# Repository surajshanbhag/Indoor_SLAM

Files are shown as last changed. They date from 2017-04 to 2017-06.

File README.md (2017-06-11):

# Indoor_SLAM

Project deals with using Raspberry Pi for Stereo Image processing in ROS.   

Please check the  doc/ folder and wiki for Documentation.

src/vision - Code for stereo streamer, receiver, synchronizer and publishing image topics to ROS  
src/control - Code for MOtor control and encoder  
src/auto_scripts - auto run scripts.    
src/model - URDF Model of the robot.

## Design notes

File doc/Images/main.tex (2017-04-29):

\documentclass[10pt]{article}
\usepackage[english]{babel}
\usepackage[utf8x]{inputenc}
\usepackage{amsmath}
\usepackage{graphicx}
\usepackage{caption}
\usepackage[colorinlistoftodos]{todonotes}
\usepackage{indentfirst}
\usepackage{geometry}
\usepackage[section]{placeins}
\usepackage{float}
\geometry{letterpaper, portrait, margin=1in}
\usepackage{hyperref}
\usepackage{subfigure}
\title{Autonomous- Final Report}
\addcontentsline{toc}{section}{References}
\begin{document}

\begin{titlepage}

\newcommand{\HRule}{\rule{\linewidth}{0.5mm}} % Defines a new command for the horizontal lines, change thickness here
\center % Center everything on the page
\textsc{\Large ECE 592-063 Introduction to Autonomous Systems}\\[1.5cm]
\HRule \\[0.4cm]
{ \huge \bfseries Final Report 

Indoor SLAM -2 using Visual SLAM}\\[0.4cm] % Title of your document
\HRule \\[1.5cm]
\begin{minipage}{0.4\textwidth}
\begin{flushleft} \large
\emph{Authors:}\\
Suraj Shanbhag % Your name

Abhishek Ravi	 % Your name

William Burdick-Crow % Your name

Siddharth Ganesh % Your name

\end{flushleft}
\end{minipage}
~
\begin{minipage}{0.4\textwidth}
\begin{flushright} \large
\emph{Mentor:} \\
Dr.Mihail L. Sichitiu % Supervisor's Name
\end{flushright}
\end{minipage}\\[0.5cm]
{\large April 23,2017}\\[2cm] 
 % Include a department/university logo - this will require the graphicx package
 
%----------------------------------------------------------------------------------------
\vfill % Fill the rest of the page with whitespace

\end{titlepage}

\tableofcontents

\listoffigures

\listoftables
\pagebreak
\section{Abstract}
	Incorporating computer vision on any system requires an immense computation power, which increases the cost and size of the system. For small robots and airborne drones it might not always be feasible to add more computation power. In this report we suggest a system where the processing of the stereo camera video feed is offloaded to a remote computer running ROS whose performance can be scaled to match the task. We use a small 2 wheeled robot with the 2 cameras and a Raspberry Pi 3 to stream the stereo video feed to the host computer which performs the tasks. Other challenges like synchronization, calibration and quality of the video are also addressed in the report. The stereo video feed received is used to create a map of the environment and help the robot navigate. This system becomes a good platform to test various Visual SLAM algorithms and we have tested ORBSLAM2 and RTAB.

\section{Introduction}
Although existing technology has made great leaps and bounds in mapping outdoor areas, it still hasn't made much progress in mapping an indoor environment. This is mainly because of the large size of the current robots being used for mapping making them un-traversable in constrained and small spaces. When such a problem arises, it is convenient if we figure out a way to map our entire surroundings so that we can have a reference to work with and make informed decisions. This problem of indoor or constrained SLAM is of extreme importance in disaster management and medical applications. By gaining real world data of these areas we can actually get an insight into the environment, be it a building debris or the inside of the intestines. By implementing visual SLAM on a two wheeled mobile robot we are presenting a case that, the robot need not be as powerful in itself to perform such high computational problems but can act as a carrier of message to a powerful system to solve real world problems.

	Currently there is very little support for using ROS to run remote slam operations. A large part of our project has been, enabling the usage of remote processing on these ROS applications. This allows for increased flexibility, both in type and cost, of the type of vehicle used for capturing images. It will also allows for a much cheaper vehicle, as all that the vehicle is responsible for is streaming the images back to the computer and controlling the robot. Due to the very few requirements that we have for the robot, it is easy to change what platform is used to carry the camera. As long as the robot is capable of streaming video, our project is applicable.

\section{Related work}
Although nobody has published their findings of Visual Stereo SLAM on a Raspberry pi, we found a work on monocular SLAM using Raspberry pi camera module.\footnote{\href{https://courses.cit.cornell.edu/ece6930/ECE6930\_Spring16\_Final\_MEng\_Reports/SLAM/Real-time\%20ROSberryPi\%20SLAM\%20Robot.pdf}{https://courses.cit.cornell.edu/ece6930/ECE6930\_Spring16\_Final\_MEng\_Reports/SLAM/Real-time\%20ROSberryPi\%20SLAM\%20Robot.pdf}}
This work basically revolves around using a raspberry pi+ camera module on a two wheeled robot of raspberry pi for loop detections and re-localization using ORBSLAM while streaming at a much low image quality for a single camera to find loop closure and odometry. Monocular SLAM can be handled by a raspberry pi, but streaming two video streams for stereo ORBSLAM is complex. There is extensive research and findings publicly available for pre-built stereo cameras but none for an assembled stereo camera setup using two monocular USB cameras. People have eliminated the use of two USB Cameras connected to a pi by using the Pi compute module. This eliminated the time synchronization issues and gives a very good image resolution.\footnote{\href{http://hackaday.com/2014/11/03/stereo-vision-and-depth-mapping-with-two-raspi-camera-modules/} {http://hackaday.com/2014/11/03/stereo-vision-and-depth-mapping-with-two-raspi-camera-modules/}} An already implemented SLAM algorithm for Stereo Outdoor mapping  \footnote{\href{http://wiki.ros.org/rtabmap\_ros}{http://wiki.ros.org/rtabmap\_ros}} served as a guide for our project to implement a low cost Indoor stereo SLAM. RTABMap (Real Time Appearance Based Mapping) is used widely to reconstruct our 3D environment. It has been deployed using a bumblebee stereo camera.\footnote{\href{http://wiki.ros.org/rtabmap\_ros/Tutorials/StereoOutdoorMapping}{http://wiki.ros.org/rtabmap\_ros/Tutorials/StereoOutdoorMapping}} 

\section{Approach}
We stated with a robot module that had two servo motors and corresponding encoders. On it we mounted the raspberry pi, two Logitech c920 web cams, a motor control hat, and a pair of power supplies (one for the pi and one for the motors). 
\subsection{Video streaming from Raspberry pi}
We started with Raspbian installed on the Pi.\footnote{\href{https://www.raspberrypi.org/downloads/raspbian/}{https://www.raspberrypi.org/downloads/raspbian/}} However, we were unable to install the uvc\_cam\footnote{\href{http://wiki.ros.org/uvc\_camera}{http://wiki.ros.org/uvc\_camera}}\footnote{\href{https://defendtheplanet.net/2014/11/05/using-ros-indigo-webcam-by-the-uvc\_camera-usb-video-class-package/}{https://defendtheplanet.net/2014/11/05/using-ros-indigo-webcam-by-the-uvc\_camera-usb-video-class-package/}} ROS package on the Rasbian OS. We then switched to a precompiled image of Ubuntu Mate\footnote{\href{http://www.german-robot.com/2016/05/26/raspberry-pi-sd-card-image/}{http://www.german-robot.com/2016/05/26/raspberry-pi-sd-card-image/}} that already had Kinetic installed. With this we were able to get the uvc\_cam to push the images to ROS and then transmit them to the computer. The issue was that, the image that we were getting was 640x480 at 3 fps with a 0.5 second delay. We then attempted to stream only gray scale. We were getting the same image at 6 fps. We determined that the issue was because ROS uses TCP, and the verifications we slowing down the video stream. To solve, this we tried to use gstreamer, motion, and flask to stream to the computer and then pass the images into ROS. However, none of these interfaced will with Kinetic. We attempted to write a UDP socket to allow the pi to stream to the computer through python. This failed. We eventually settled on using a modified version of the v4l2 driver by Joakim Nohlgård\footnote{\href{https://github.com/gebart/python-v4l2capture}{https://github.com/gebart/python-v4l2capture}}. With this we were able to stream 1280x720 at 30fps for a single feed and  800x600 at 30fps for a stereo stream. 
\begin{figure*}[!h]
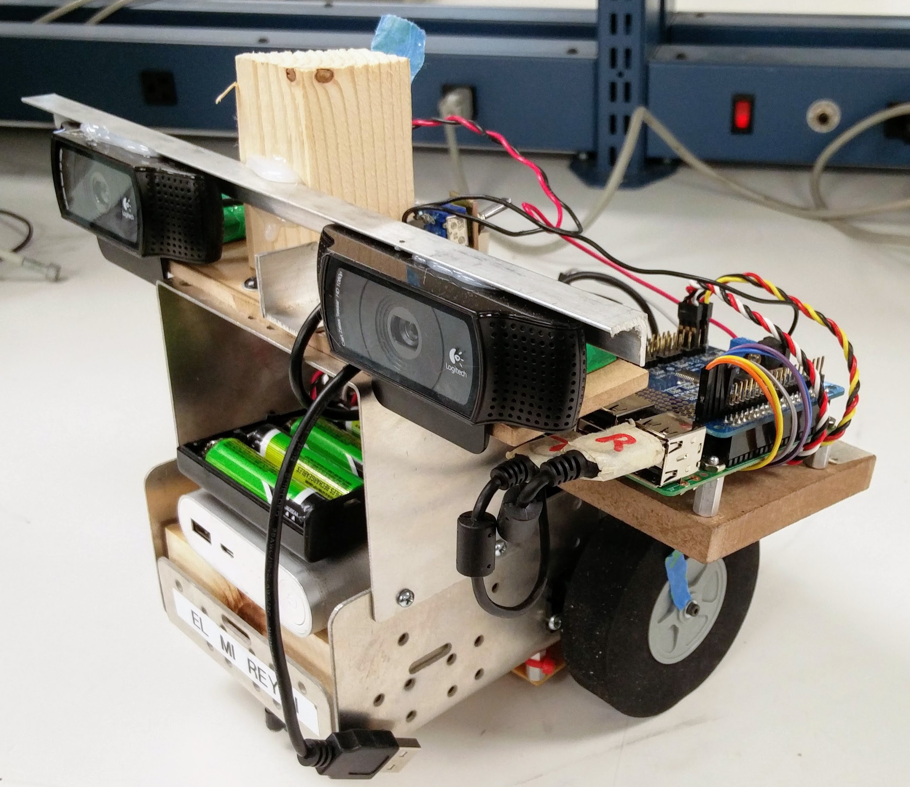
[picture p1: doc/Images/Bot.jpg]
\centering 
\caption{The Robot with 2 logitech webcams connected to  Raspberry Pi 3}
\end{figure*}
This solved our streaming issue. However, we now experienced a intermittent broken pipe error when starting the streaming. The issue would appear occasionally and only ever when starting the cameras. We attempted switching what USB ports we were using, what order the cameras were plugged in, and changing the camera, with no result. When we switched Pis we saw a decreases in events but not a total fix. Eventually we narrowed the issue down to a power spike when the camera was initialized causing the voltage on the USBs to sag resulting in the second camera failing. This issue can be avoided by waiting at least 20 seconds for the first camera to finish initializing before you start the second. 
\subsection{Camera Calibration and Synchronization}
Now that we had functioning streaming, we calibrated the cameras using the ROS camera\_calibration package \footnote{\href{http://wiki.ros.org/camera\_calibration}{http://wiki.ros.org/camera\_calibration}}. We then published the calibration files to ROS along with the video streams. Then we ran ORB\_SLAM2\footnote{\href{https://github.com/raulmur/ORB_SLAM2}{https://github.com/raulmur/ORB\_SLAM2}}, it successfully localized the robot, found loop closure, providing trajectory, and creating a point cloud. Next we moved on to trying to run RTAB-Map.\footnote{\href{https://introlab.github.io/rtabmap/}{https://introlab.github.io/rtabmap/}} To do this we had to run stereo\_image\_proc \footnote{\href{http://wiki.ros.org/stereo\_image\_proc}{http://wiki.ros.org/stereo\_image\_proc}} package which takes in the published stereo images and corresponding camera info and to produce rectified images, gray scale images, disparity images, and a point cloud. These are passed into RTAB which uses these and the odometry to create a map of its surroundings. Stereo\_image\_proc would not run because our left and right camera images were not synchronized. To resolve this we tried a number of modifications to our streamer. First we tried to combined the videos on the Pi and then stream them as one object, so that when they were passed into ROS they would arrive at the same time. This failed because the memory buffer allocation failed. Next we tried to use multi treading to simultaneously stream the two videos. This failed because pythons multi threading capabilities were insufficient for the heavy load. Then we progressed to the receiver. Initially we attempted to synchronize the files by re-writing the python socket receiver so that it captured the the two frames simultaneously and then passed them into ROS as one object. This failed because trying to synchronize the frame receptions was causing the stream to lag. Next, we tried to alternate the reception of the packets from both frames in the same sequentially we attempted to use the ROS message\_filter package executed script and then publish them once both were received. This failed because when receiving the frames one would block the other resulting in many incomplete frame and inconsistent image quality. Next \footnote{\href{http://wiki.ros.org/message\_filters}{http://wiki.ros.org/message\_filters}}, this did not sufficiently synchronize the images. Finally, we managed to synchronize the images by waiting until they were published into ROS, by separate receivers, and then editing the time stamp to be the same value.
\begin{figure*}[!h]
\centering \label{Occupancy Grid Created}
\caption{Occupancy Grid Created}
\end{figure*}
\subsection{SLAM and Hardware}
Once the synchronization was achieved stereo\_image\_proc worked but resulted in an image that was more distorted than the raw image. However, now that we had stereo\_image\_proc functioning we attempted to run RTAB. RTAB requires transformations from the fixed frame of the robot to the camera. For this we used an Unified Robot Description Format file. URDF is an XML format for representing a robot model. We use this file to accurately describe the robot in space, for finding the transformations between different links in the robot, and for finding the correlation between different frames of references. We also added support for the encoders. The encoder values are read using an ADC connected to the Raspberry Pi. Using motors controlled by a joystick, we were able to test the accuracy of the encoders by moving the robot in a pattern. When working with the encoders, we had an issues with the numbers increasing when the robot was not moving. To resolve this we required two reading of each color before registering a color change. After testing, we determined that the encoders were not accurate enough for our application, so we increased the number of divisions on the encoder wheels from 20 to 40. Also RTAB requires that the images be associated with a link in the robot transform. We added functionality to the synchronization node to update the associated link in the ROS message being published. 

\begin{figure*}[!h]
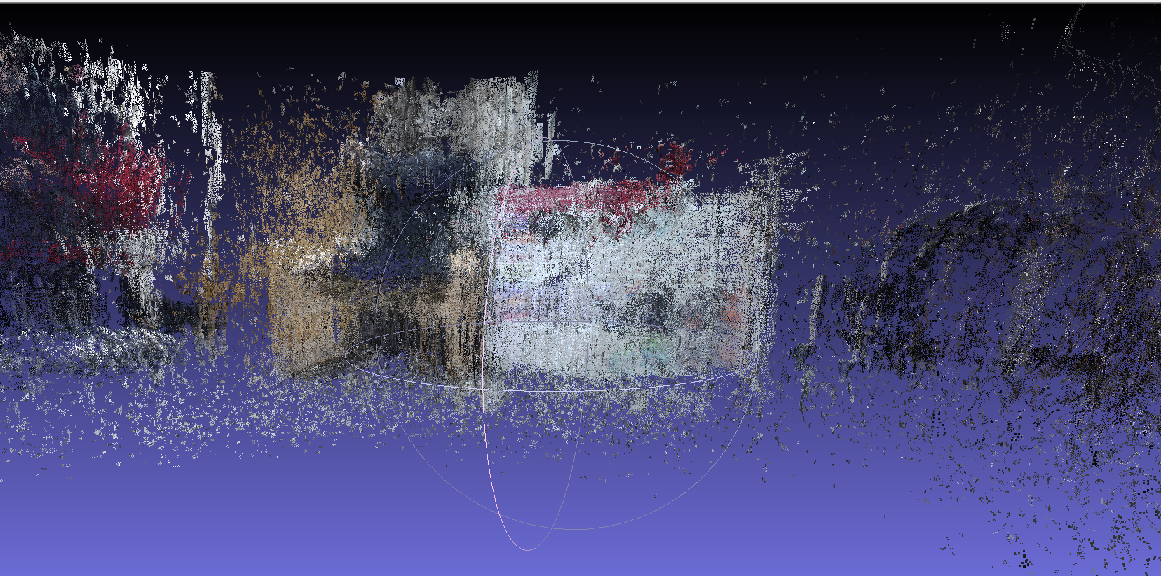
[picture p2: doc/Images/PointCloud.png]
\centering \label{Point Cloud}
\caption{Point Cloud of Chair and Poster as seen by the robot}
\end{figure*}

We ran RTAB which resulted in a poor point cloud, so we re- calibrated the cameras using a larger and more precise checkerboard. During this process, one of the motors and one of the encoders failed. We replaced the motor and encoder. We tweaked the settings of the stereo\_image\_proc package to produce the best possible point cloud from the disparity in the stereo images. We were able to get a good point cloud and an average occupancy grid.(Figure 3)

\section{Experimental Results and Analysis}
\subsection{Video streaming from Raspberry pi}
	At the beginning of the project we started with ROS uvc\_camera package to stream the stereo feed to the personal computer. However , as ROS uses TCP protocol the video stream had bad performance and can be seen in the table below. The stream received was synchronized but was not good enough to run any real time algorithms as it was delayed by about 2s. One of the counter measures taken was to use gray scale images, as the SLAM algorithms do not make use of the color information in the images. The frame rate increased to 5 fps, however the delay was still the same. We then switched to UDP based streaming programs and used v4l2 based streamer. This yielded extremely good results with 800x600 images being streamed at 30FPS and a delay of less than 0.5s. However the synchronization between the frames was lost and we had to handle the synchronization at the receiver using another buffer ROS program.
\begin{figure}[H]
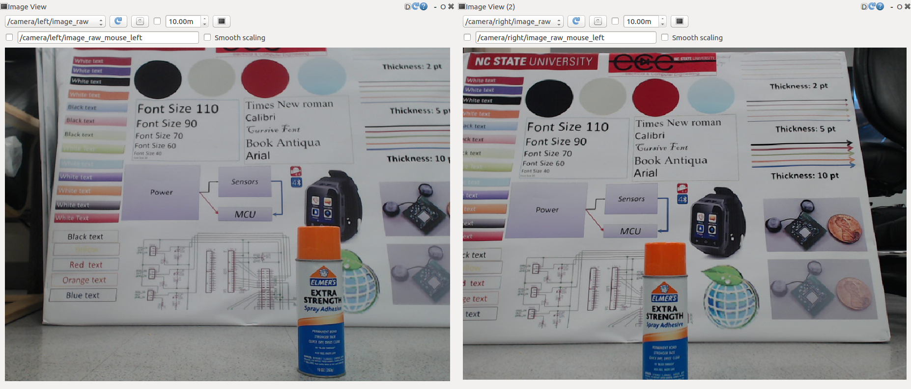
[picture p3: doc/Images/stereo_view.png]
\centering \label{Stereo video feed}
\caption{Stereo video feed}
\end{figure}
\begin{table}[H]
\begin{center}
\begin{tabular}{|c|c|c|c|c|c|}
\hline
Method &FPS & Delay & Image Size & Image Consistency & Synchronization\\[1ex]
\hline
ROS uvc\_camera & 3 & 2s & 640x480 & Good & Yes\\ [1ex]
\hline 
ROS uvc\_camera Gray scale images& 5 & 2s & 640x480 & Good & Yes\\ [1ex]
\hline 
self-made UDP socket& 0 & $\infty$s & 640x480 & Bad & No\\ [1ex]
\hline 
v4l2 driver & 30 & \textless 0.5s  & 800x600 & Good & No\\ [1ex]
\hline

\end{tabular}
\caption{Stream method analysis}
\end{center}
\end{table}

\subsection{Experiments with Encoders}
When testing for the accuracy of our odometry, we noticed that the encoder values increased when the robot was stationary. In response we checked to ensure that we get multiple consistent encoder readings before registering a color change. We would still occasionally get the number increasing very rapidly. We determined that is was the result of the encoder stopping on the devision between white and black, resulting in the value being right around the threshold. To resolve this we inserted a 'dead band' which is considered neither white nor black. We also had issues with the encoders not accurately measuring turns, so we decided to create our own encoder wheel to suit our application. Hence, the 20 division encoder was replaced with a 40 devision encoder wheel. This setup increased the resolution of the encoders and allowed the odometry to consistently measure turns.     
\begin{figure}[H]
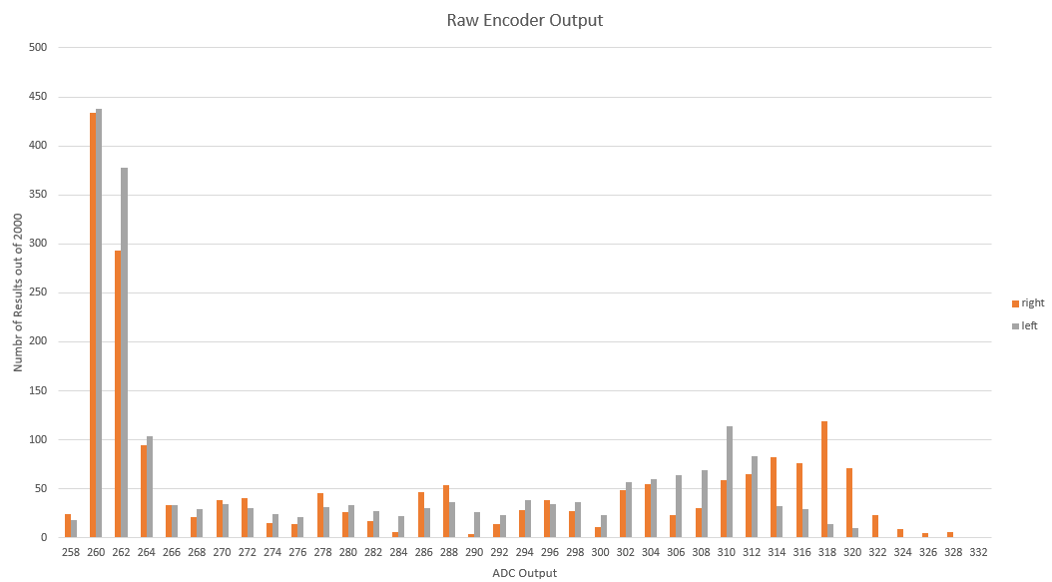
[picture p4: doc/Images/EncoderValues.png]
\centering \label{Encoder values}
\caption{Histogram Encoder values}
\end{figure}

\subsection{Camera Calibration Results}
	Calibration of images is one of the most important part of any computer vision applications. This process yields a list of values which are used to correct the image of distortions due to the inherent defects in the sensor and lenses. One of the common ways of calibration is to use a checkerboard pattern and estimate the parameters based on the corners in the checkerboard. The number and size of square are input to the calibration function. We have used the ROS calibration program to do this. We first tried the calibration using a 9x7 checkerboard with 25mm squares. The results were not as good and can be seen in Figure 6. The calibration was repeated with a big checkerboard with 9x6 113mm squares. The result is a good rectified image as can be seen in Figure 7. The result is not perfect and requires fixing both web cameras onto a single platform and ensuring there is no motion relative to each other. The current calibration was done using 39 image pairs. Higher number of images yield better results but take significantly longer time.
    
\begin{figure}[H]
\centering \label{Chekerboard}
\caption{Calibration in Progress, detected Checkerboard corners are highlighted by program}
\end{figure}

\begin{figure}[H]
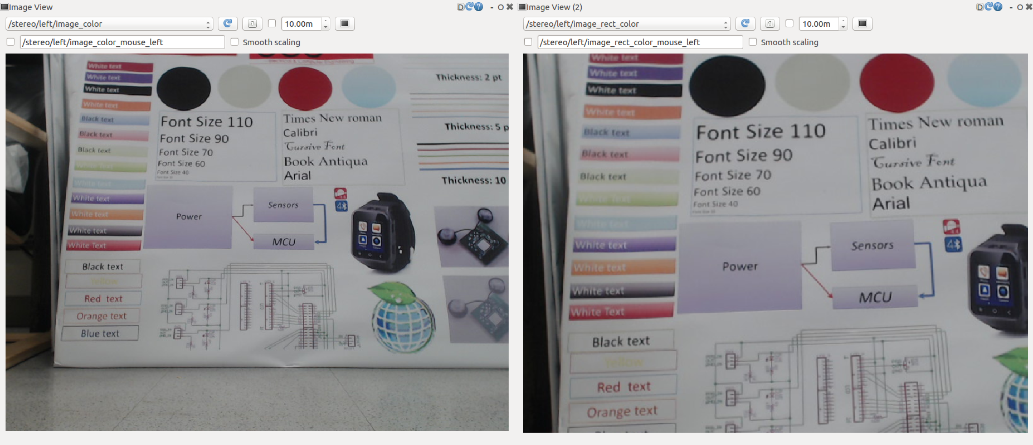
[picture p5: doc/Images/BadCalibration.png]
\centering \label{Result Bad Calibration}
\caption{Poor Calibration , right image is the rectified image of the left image}
\end{figure}

\begin{figure}[H]
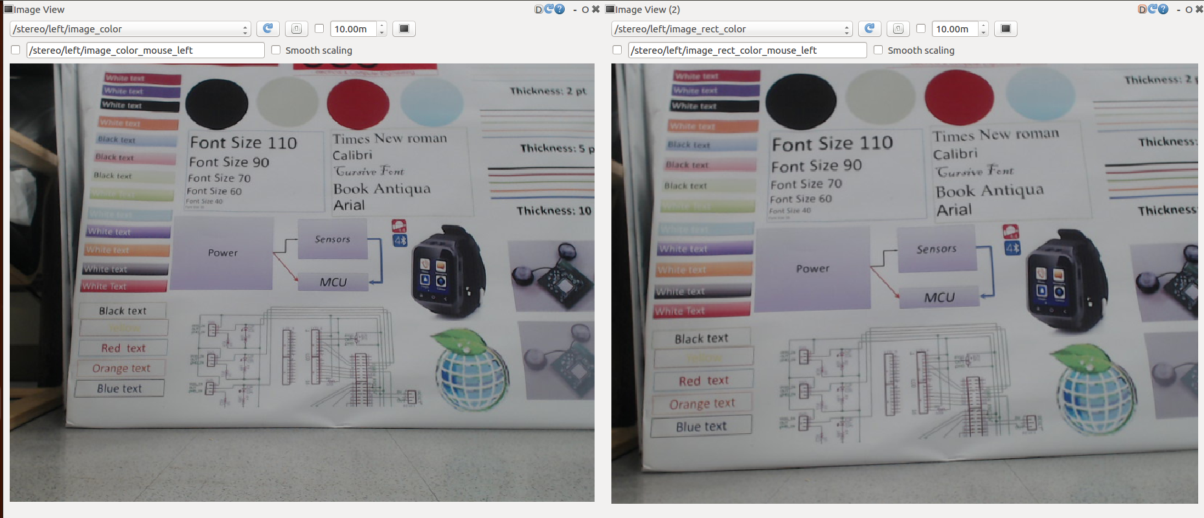
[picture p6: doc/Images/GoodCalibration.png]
\centering \label{Result Good Calibration}
\caption{Good Calibration , right image is the rectified image of the left image}
\end{figure}

\subsection{Stereo\_Image\_Proc Calibration Results}
Stereo\_Image\_Proc is used to produce a disparity image by comparing the right and left camera stream. By adjusting the perimeters it uses you can tailor the setting to fit your objective. These allow for you to filter out noise in the environment, control the sensitivity to texture, and control the intended focus length of the cameras. In figure 9 you can see the improvement after fine tuning of these settings.    
\begin{figure}[H]
\hfill
\subfigure[Initial Stereo\_Image\_Proc Point Cloud]{}
\hfill
\subfigure[Final Stereo\_Image\_Proc Point Cloud]{}
\hfill
\caption{Initial Stereo\_Image\_Proc Calibration}
\end{figure}

\subsection{ORB SLAM Results}
	With the Stereo feed available we tested ORBSLAM2. ORBSLAM2 is well known for robustness,good localization and real-time performance. However the point cloud generated was not good and the environment cannot be known. With our setup we were able to get a good loop  closure and odometry and can be used to supplement wheel odometry.The results can be seen in Figure  11.\footnote{\href{https://www.youtube.com/watch?v=LTfOwyYde9E}{https://www.youtube.com/watch?v=LTfOwyYde9E}}
\begin{figure}[H]
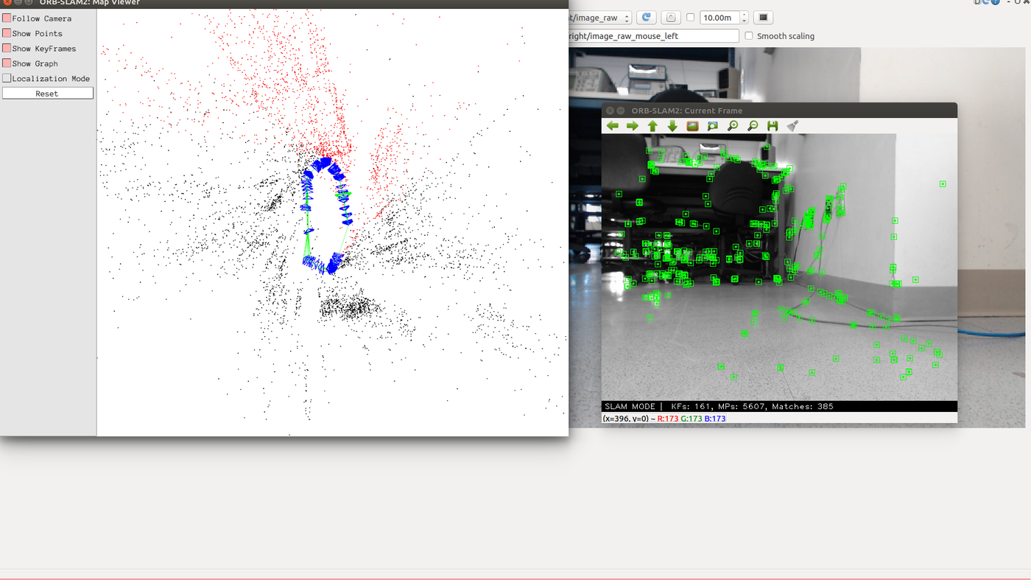
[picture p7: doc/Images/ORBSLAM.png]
\centering \label{ORBSLAM2}
\caption{loop closure with ORBSLAM}
\end{figure}

\subsection{RTAB Map Results}
	While ORBSLAM can provide good and robust Odometry in realtime, RTAB can create a good 3D point cloud of the environment and a occupancy grid. It does this by using rectified images from stereo\_image\_proc and odometry. It projects the point onto a plane to create a occupancy grid. The settings for the height of obstacle can be changed and only objects of certain height can be treated ass obstacles. The occupancy grid created can be used for navigation.
\begin{figure}[H]
\centering \label{PointCloud of RTAB}
\caption{Point Cloud of RTAB shows a chair on the side and a poster beside it rendered in 3D.}
\end{figure}
\begin{figure}[H]
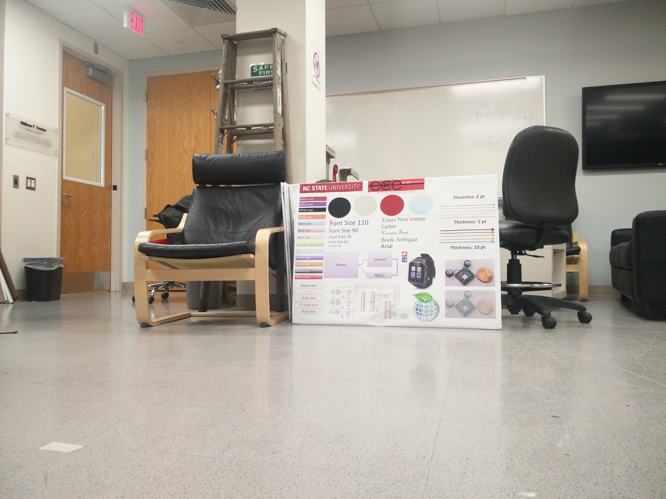
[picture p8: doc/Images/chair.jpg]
\centering \label{Point Cloud Image}
\caption{The scene reconstructed by RTAB.}
\end{figure}
\begin{figure}[H]
\centering \label{Occupancy Grid}
\caption{Occupancy Grid created using RTAB. The black color indicates obstacles and rest is traversable space}
\end{figure}

\pagebreak
\section{Conclusion}
The problem statement was to implement a low cost Indoor SLAM for scanning an indoor area using a camera(s) and create a 3D reconstruction of its environment and also to create an occupancy grid or a traversable map. We were able to transform a two wheeled robot skeleton with motors and wheels into a robotic platform to stream stereo images to a remote computer and capable of controlling the motors on receiving commands form the remote computer. We were able to recreate the environment around the robot as a three dimensional point cloud. To achieve this level of performance, we had to create our own stereo camera rig using two monocular USB cameras. We implemented a python socket program to stream the video feed. We have implemented two SLAM techniques and compared their results for our robotic setup. 
%\pagebreak
\section{Appendices}
\subsection{GitHub repository}

All source code and instructions to recreate the project can be accessed from the GitHub repository Indoor\_SLAM \href{https://github.com/surajshanbhag/Indoor\_SLAM.git}{https://github.com/surajshanbhag/Indoor\_SLAM.git}
\subsection{Supplementary Images}
\begin{figure}[H]
\hfill
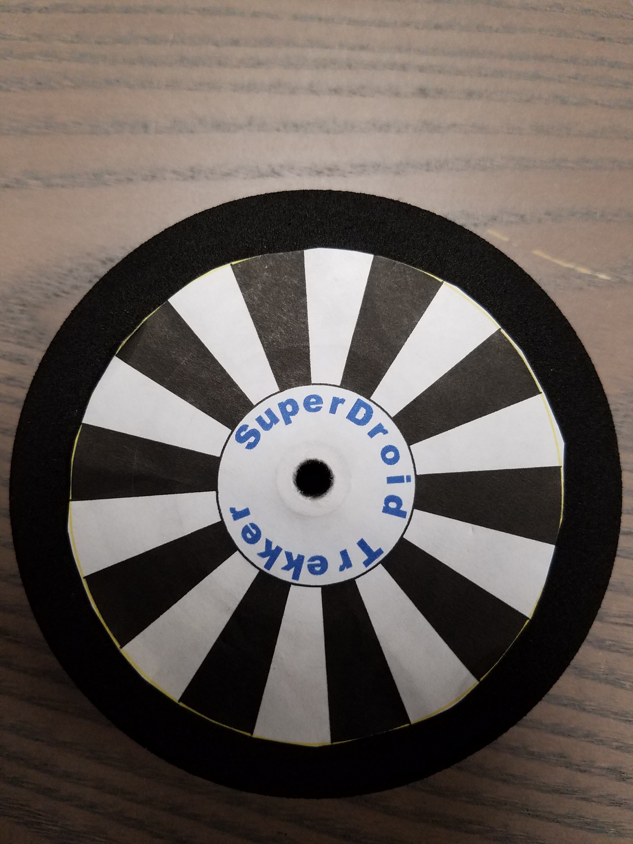
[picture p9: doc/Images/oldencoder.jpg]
\subfigure[Old encoder]{}
\hfill
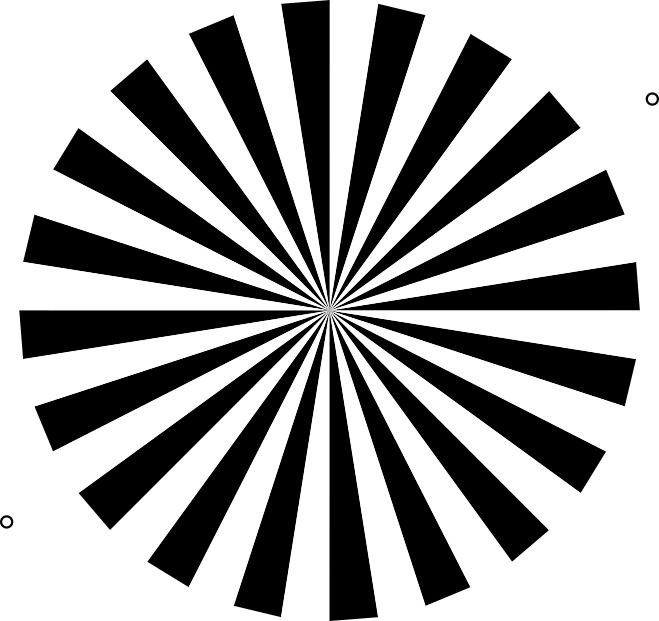
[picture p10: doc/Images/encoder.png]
\subfigure[New encoder]{}
\hfill
\caption{Encoder stripes}
\end{figure}
\begin{figure}[H]
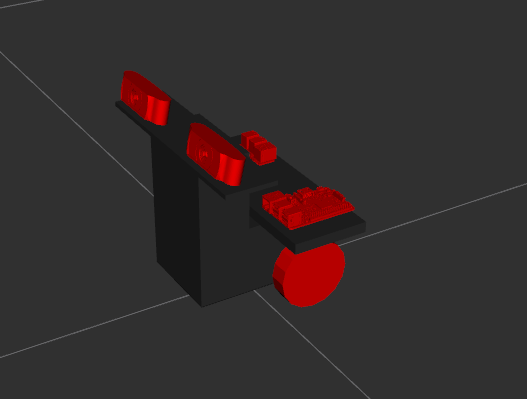
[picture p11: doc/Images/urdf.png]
\centering \label{URDF Model}
\caption{URDF Model created for the project. Provides frame of references and transformation between wheels, cameras and the base of the robot.}
\end{figure}
\bibliographystyle{unsrt}
\end{document}

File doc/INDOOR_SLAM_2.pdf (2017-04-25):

ECE 592-063 Introduction to Autonomous Systems

# Final Report Indoor SLAM -2 using Visual SLAM

Authors:
Suraj Shanbhag
Abhishek Ravi
William Burdick-Crow
Siddharth Ganesh

Mentor:
Dr.Mihail L. Sichitiu

April 23,2017

## Contents

References | 1
1 Abstract | 2
2 Introduction | 2
3 Related work | 2
4 Approach | 3
4.1 Video streaming from Raspberry pi | | 3
4.2 Camera Calibration and Synchronization | | 4
4.3 SLAM and Hardware | | 4
5 Experimental Results and Analysis | 5
5.1 Video streaming from Raspberry pi | | 5
5.2 Experiments with Encoders | | 6
5.3 Camera Calibration Results | | 7
5.4 Stereo Image Proc Calibration Results | | 8
5.5 ORB SLAM Results | | 8
5.6 RTAB Map Results | | 9
6 Conclusion | 11
7 Appendices | 11
7.1 GitHub repository | | 11
7.2 Supplementary Images | | 11

## List of Figures

1 | The Robot with 2 logitech webcams connected to Raspberry Pi 3 | | 3
2 | Occupancy Grid Created | | 4
3 | Point Cloud of Chair and Poster as seen by the robot | | 5
4 | Stereo video feed | | 6
5 | Histogram Encoder values | | 6
6 | Calibration in Progress, detected Checkerboard corners are highlighted by program | | 7
7 | Poor Calibration , right image is the rectified image of the left image | | 7
8 | Good Calibration , right image is the rectified image of the left image | | 8
9 | Initial Stereo Image Proc Calibration | | 8
10 | loop closure with ORBSLAM | | 9
11 | Point Cloud of RTAB shows a chair on the side and a poster beside it rendered in 3D | | 9
12 | The scene reconstructed by RTAB | | 10
13 | Occupancy Grid created using RTAB. The black color indicates obstacles and rest is traversable
| space | | 10
14 | Encoder stripes | | 11
15 | URDF Model created for the project. Provides frame of references and transformation between
| wheels, cameras and the base of the robot | | 12

## List of Tables

1 | Stream method analysis | | 6

## 1 Abstract

Incorporating computer vision on any system requires an immense computation power, which increases the cost and size of the system. For small robots and airborne drones it might not always be feasible to add more computation power. In this report we suggest a system where the processing of the stereo camera video feed is offloaded to a remote computer running ROS whose performance can be scaled to match the task. We use a small 2 wheeled robot with the 2 cameras and a Raspberry Pi 3 to stream the stereo video feed to the host computer which performs the tasks. Other challenges like synchronization, calibration and quality of the video are also addressed in the report. The stereo video feed received is used to create a map of the environment and help the robot navigate. This system becomes a good platform to test various Visual SLAM algorithms and we have tested ORBSLAM2 and RTAB.

## 2 Introduction

Although existing technology has made great leaps and bounds in mapping outdoor areas, it still hasn’t made much progress in mapping an indoor environment. This is mainly because of the large size of the current robots being used for mapping making them un-traversable in constrained and small spaces. When such a problem arises, it is convenient if we figure out a way to map our entire surroundings so that we can have a reference to work with and make informed decisions. This problem of indoor or constrained SLAM is of extreme importance in disaster management and medical applications. By gaining real world data of these areas we can actually get an insight into the environment, be it a building debris or the inside of the intestines. By implementing visual SLAM on a two wheeled mobile robot we are presenting a case that, the robot need not be as powerful in itself to perform such high computational problems but can act as a carrier of message to a powerful system to solve real world problems.
Currently there is very little support for using ROS to run remote slam operations. A large part of our project has been, enabling the usage of remote processing on these ROS applications. This allows for increased flexibility, both in type and cost, of the type of vehicle used for capturing images. It will also allows for a much cheaper vehicle, as all that the vehicle is responsible for is streaming the images back to the computer and controlling the robot. Due to the very few requirements that we have for the robot, it is easy to change what platform is used to carry the camera. As long as the robot is capable of streaming video, our project is applicable.

## 3 Related work

Although nobody has published their findings of Visual Stereo SLAM on a Raspberry pi, we found a work on monocular SLAM using Raspberry pi camera module.¹ This work basically revolves around using a raspberry pi+ camera module on a two wheeled robot of raspberry pi for loop detections and re-localization using ORBSLAM while streaming at a much low image quality for a single camera to find loop closure and odometry. Monocular SLAM can be handled by a raspberry pi, but streaming two video streams for stereo ORBSLAM is complex. There is extensive research and findings publicly available for pre-built stereo cameras but none for an assembled stereo camera setup using two monocular USB cameras. People have eliminated the use of two USB Cameras connected to a pi by using the Pi compute module. This eliminated the time synchronization issues and gives a very good image resolution.² An already implemented SLAM algorithm for Stereo Outdoor mapping 3
served as a guide for our project to implement a low cost Indoor stereo SLAM. RTABMap (Real Time Appearance Based Mapping) is used widely to reconstruct our 3D environment. It has been deployed using a bumblebee stereo camera.⁴

1https://courses.cit.cornell.edu/ece6930/ECE6930 Spring16 Final MEng Reports/SLAM/Realtime%20ROSberryPi%20SLAM%20Robot.pdf (https://courses.cit.cornell.edu/ece6930/ECE6930_Spring16_Final_MEng_Reports/SLAM/Real-time%20ROSberryPi%20SLAM%20Robot.pdf) 2http://hackaday.com/2014/11/03/stereo-vision-and-depth-mapping-with-two-raspi-camera-modules/3http://wiki.ros.org/rtabmap ros (http://wiki.ros.org/rtabmap_ros)
4http://wiki.ros.org/rtabmap ros/Tutorials/StereoOutdoorMapping (http://wiki.ros.org/rtabmap_ros/Tutorials/StereoOutdoorMapping)

## 4 Approach

We stated with a robot module that had two servo motors and corresponding encoders. On it we mounted the raspberry pi, two Logitech c920 web cams, a motor control hat, and a pair of power supplies (one for the pi and one for the motors).

### 4.1 Video streaming from Raspberry pi

We started with Raspbian installed on the Pi.⁵ However, we were unable to install the uvc cam⁶⁷ ROS package on the Rasbian OS. We then switched to a precompiled image of Ubuntu Mate⁸
that already had
Kinetic installed. With this we were able to get the uvc cam to push the images to ROS and then transmit them to the computer. The issue was that, the image that we were getting was 640x480 at 3 fps with a 0.5 second delay. We then attempted to stream only gray scale. We were getting the same image at 6 fbs. We determined that the issue was because ROS uses TCP, and the verifications we slowing down the video stream. To solve, this we tried to use gstreamer, motion, and flask to stream to the computer and then pass the images into ROs. However, none of these interfaced will with Kinetic. We attempted to write a UDP socket to allow the pi to stream to the computer through python. This failed. We eventually settled on using a modified version of the v4l2 driver by Joakim Nohlg˚ard⁹
. With this we were able to stream 1280x720 at 30fps for a single feed and 800x600 at 30fps for a stereo stream. This solved our streaming issue. However,

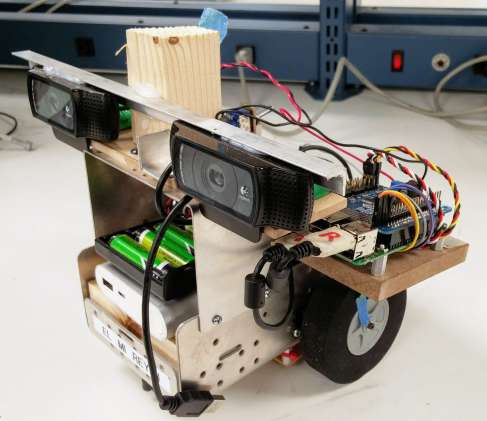
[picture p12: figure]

Figure 1: The Robot with 2 logitech webcams connected to Raspberry Pi 3

we now experienced a intermittent broken pipe error when starting the streaming. The issue would appear occasionally and only ever when starting the cameras. We attempted switching what USB ports we were using, what order the cameras were plugged in, and changing the camera, with no result. When we switched Pis we saw a decreases in events but not a total fix. Eventually we narrowed the issue down to a power spike when the camera was initialized causing the voltage on the USBs to sag resulting in the second camera failing. This issue can be avoided by waiting at least 20 seconds for the first camera to finish initializing before you start the second.

5https://www.raspberrypi.org/downloads/raspbian/
6http://wiki.ros.org/uvc camera (http://wiki.ros.org/uvc_camera)
7https://defendtheplanet.net/2014/11/05/using-ros-indigo-webcam-by-the-uvc camera-usb-video-class-package/ 8http://www.german-robot.com/2016/05/26/raspberry-pi-sd-card-image/9https://github.com/gebart/python-v4l2capture

### 4.2 Camera Calibration and Synchronization

Now that we had functioning streaming, we calibrated the cameras using the ROS camera calibration package 10. We then published the calibration files to ROS along with the video streams. Then we ran ORB SLAM2¹¹, it successfully localized the robot, found loop closure, providing trajectory, and creating a point cloud. Next we moved on to trying to run RTAB-Map.¹² To do this we had to run stereo image proc 13 package which takes in the published stereo images and corresponding camera info and to produce rectified images, gray scale images, disparity images, and a point cloud. These are passed into RTAB which uses these and the odometry to create a map of its surroundings. Stereo image proc would not run because our left and right camera images were not synchronized. To resolve this we tried a number of modifications to our streamer. First we tried to combined the videos on the Pi and then stream them as one object, so that when they were passed into ROS they would arrive at the same time. This failed because the memory buffer allocation failed. Next we tried to use multi treading to simultaneously stream the two videos. This failed because pythons multi threading capabilities were insufficient for the heavy load. Then we progressed to the receiver. Initially we attempted to synchronize the files by re-writing the python socket receiver so that it captured the the two frames simultaneously and then passed them into ROS as one object. This failed because trying to synchronize the frame receptions was causing the stream to lag. Next, we tried to alternate the reception of the packets from both frames in the same sequentially executed script and then publish them once both were received. This failed because when receiving the frames one would block the other resulting in many incomplete frame and inconsistent image quality. Next we attempted to use the ROS message filter package 14, this did not sufficiently synchronize the images. Finally, we managed to synchronize the images by waiting until they were published into ROS, by separate receivers, and then editing the time stamp to be the same value.

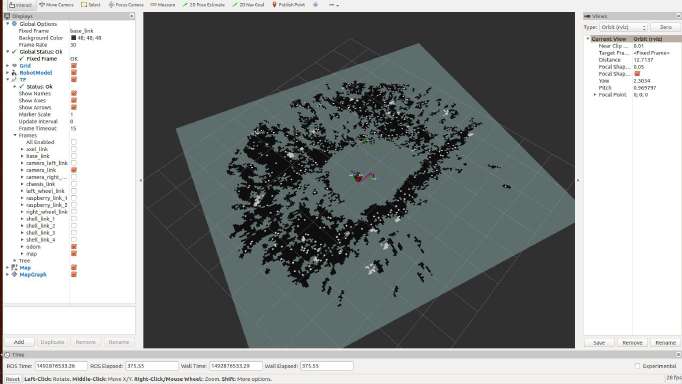
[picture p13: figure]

Figure 2: Occupancy Grid Created

### 4.3 SLAM and Hardware

Once the synchronization was achieved stereo image proc worked but resulted in an image that was more distorted than the raw image. However, now that we had stereo image proc functioning we attempted to run RTAB. RTAB requires transformations from the fixed frame of the robot to the camera. For this we used an Unified Robot Description Format file. URDF is an XML format for representing a robot model. We use this file to accurately describe the robot in space, for finding the transformations between different links

10http://wiki.ros.org/camera calibration (http://wiki.ros.org/camera_calibration)
11https://github.com/raulmur/ORB SLAM2 (https://github.com/raulmur/ORB_SLAM2)
12https://introlab.github.io/rtabmap/13http://wiki.ros.org/stereo image proc (http://wiki.ros.org/stereo_image_proc) 14http://wiki.ros.org/message filters (http://wiki.ros.org/message_filters)

in the robot, and for finding the correlation between different frames of references. We also added support for the encoders. The encoder values are read using an ADC connected to the Raspberry Pi. Using motors controlled by a joystick, we were able to test the accuracy of the encoders by moving the robot in a pattern. When working with the encoders, we had an issues with the numbers increasing when the robot was not moving. To resolve this we required two reading of each color before registering a color change. After testing, we determined that the encoders were not accurate enough for our application, so we increased the number of divisions on the encoder wheels from 20 to 40. Also RTAB requires that the images be associated with a link in the robot transform. We added functionality to the synchronization node to update the associated link in the ROS message being published.

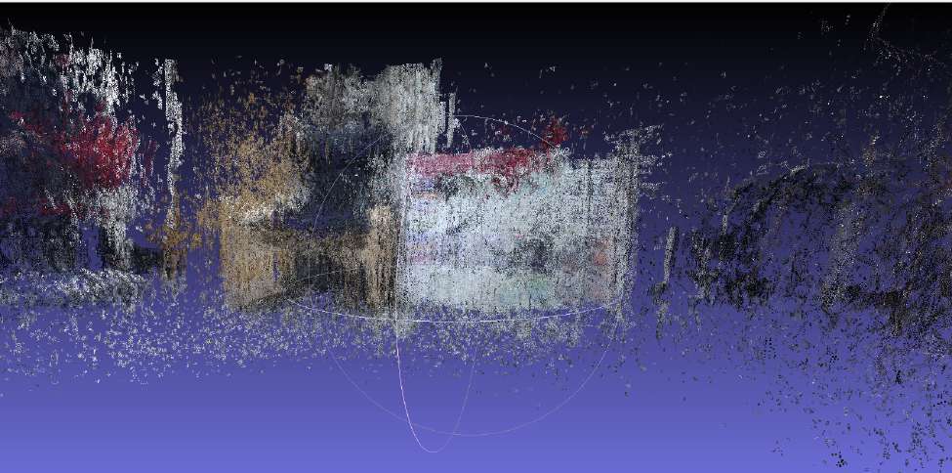
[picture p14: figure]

Figure 3: Point Cloud of Chair and Poster as seen by the robot

We ran RTAB which resulted in a poor point cloud, so we re- calibrated the cameras using a larger and more precise checkerboard. During this process, one of the motors and one of the encoders failed. We replaced the motor and encoder. We tweaked the settings of the stereo image proc package to produce the best possible point cloud from the disparity in the stereo images. We were able to get a good point cloud and an average occupancy grid.(Figure 3)

## 5 Experimental Results and Analysis

### 5.1 Video streaming from Raspberry pi

At the beginning of the project we started with ROS uvc camera package to stream the stereo feed to the personal computer. However , as ROS uses TCP protocol the video stream had bad performance and can be seen in the table below. The stream received was synchronized but was not good enough to run any real time algorithms as it was delayed by about 2s. One of the counter measures taken was to use gray scale images, as the SLAM algorithms do not make use of the color information in the images. The frame rate increased to 5 fps, however the delay was still the same. We then switched to UDP based streaming programs and used v4l2 based streamer. This yielded extremely good results with 800x600 images being streamed at 30FPS and a delay of less than 0.5s. However the synchronization between the frames was lost and we had to handle the synchronization at the receiver using another buffer ROS program.

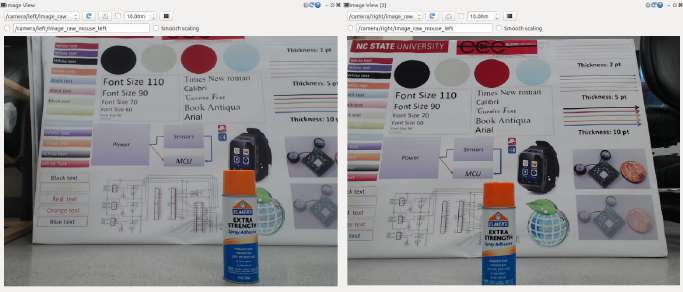
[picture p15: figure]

Figure 4: Stereo video feed

Method | FPS | Delay | Image Size | Image Consistency | Synchronization
ROS uvc camera | 3 | 2s | 640x480 | Good | Yes
ROS uvc camera Gray scale images | 5 | 2s | 640x480 | Good | Yes
self-made UDP socket | 0 | ∞s | 640x480 | Bad | No
v4l2 driver | 30 | <0.5s | 800x600 | Good | No

Table 1: Stream method analysis

### 5.2 Experiments with Encoders

When testing for the accuracy of our odometry, we noticed that the encoder values increased when the robot was stationary. In response we checked to ensure that we get multiple consistent encoder readings before registering a color change. We would still occasionally get the number increasing very rapidly. We determined that is was the result of the encoder stopping on the devision between white and black, resulting in the value being right around the threshold. To resolve this we inserted a ’dead band’ which is considered neither white nor black. We also had issues with the encoders not accurately measuring turns, so we decided to create our own encoder wheel to suit our application. Hence, the 20 division encoder was replaced with a 40 devision encoder wheel. This setup increased the resolution of the encoders and allowed the odometry to consistently measure turns.

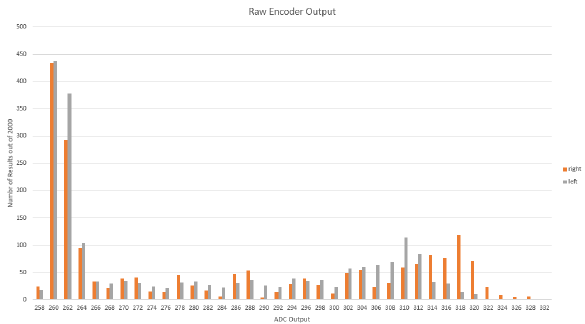
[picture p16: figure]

Figure 5: Histogram Encoder values

### 5.3 Camera Calibration Results

Calibration of images is one of the most important part of any computer vision applications. This process yields a list of values which are used to correct the image of distortions due to the inherent defects in the sensor and lenses. One of the common ways of calibration is to use a checkerboard pattern and estimate the parameters based on the corners in the checkerboard. The number and size of square are input to the calibration function. We have used the ROS calibration program to do this. We first tried the calibration using a 9x7 checkerboard with 25mm squares. The results were not as good and can be seen in Figure 6. The calibration was repeated with a big checkerboard with 9x6 113mm squares. The result is a good rectified image as can be seen in Figure 7. The result is not perfect and requires fixing both web cameras onto a single platform and ensuring there is no motion relative to each other. The current calibration was done using 39 image pairs. Higher number of images yield better results but take significantly longer time.

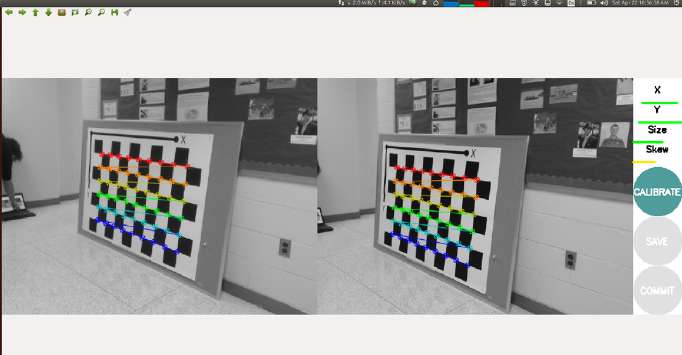
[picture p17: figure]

Figure 6: Calibration in Progress, detected Checkerboard corners are highlighted by program

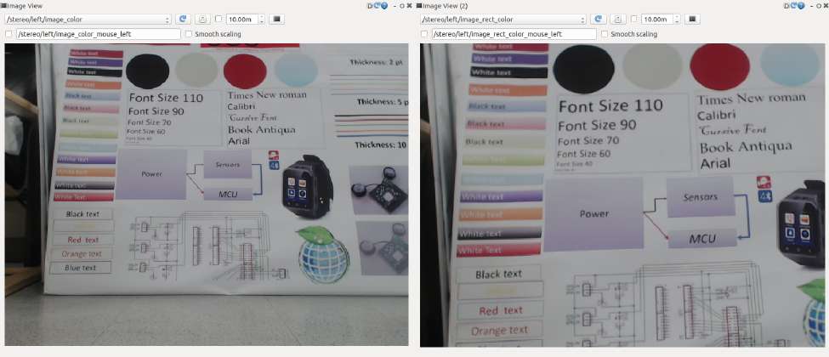
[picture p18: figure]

Figure 7: Poor Calibration , right image is the rectified image of the left image

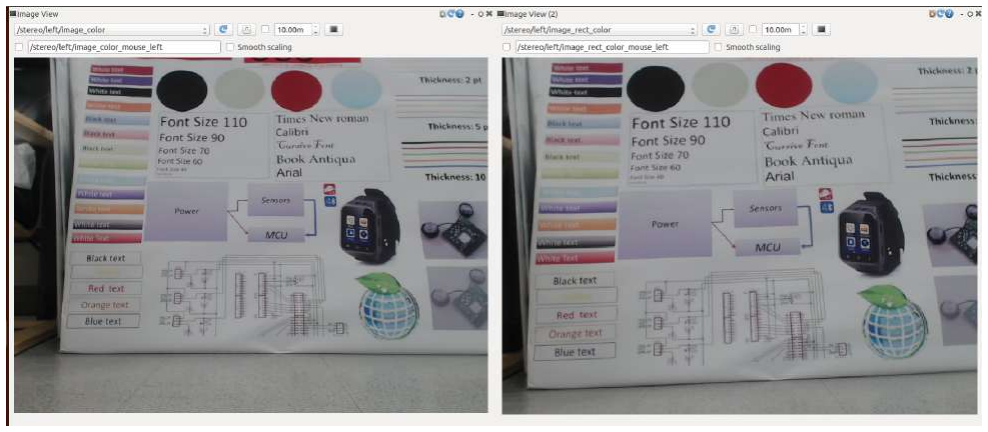
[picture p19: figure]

Figure 8: Good Calibration , right image is the rectified image of the left image

### 5.4 Stereo Image Proc Calibration Results

Stereo Image Proc is used to produce a disparity image by comparing the right and left camera stream. By adjusting the perimeters it uses you can tailor the setting to fit your objective. These allow for you to filter out noise in the environment, control the sensitivity to texture, and control the intended focus length of the cameras. In figure 9 you can see the improvement after fine tuning of these settings.

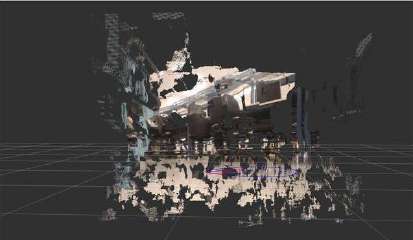
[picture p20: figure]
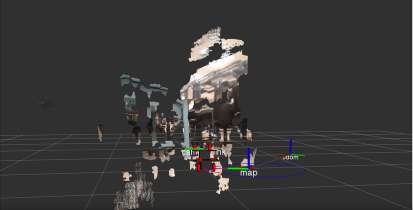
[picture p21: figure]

(a) Initial Stereo Image Proc Point Cloud | (b) Final Stereo Image Proc Point Cloud

Figure 9: Initial Stereo Image Proc Calibration

### 5.5 ORB SLAM Results

With the Stereo feed available we tested ORBSLAM2. ORBSLAM2 is well known for robustness,good localization and real-time performance. However the point cloud generated was not good and the environment cannot be known. With our setup we were able to get a good loop closure and odometry and can be used to supplement wheel odometry.The results can be seen in Figure 11.¹⁵

15https://www.youtube.com/watch?v=LTfOwyYde9E

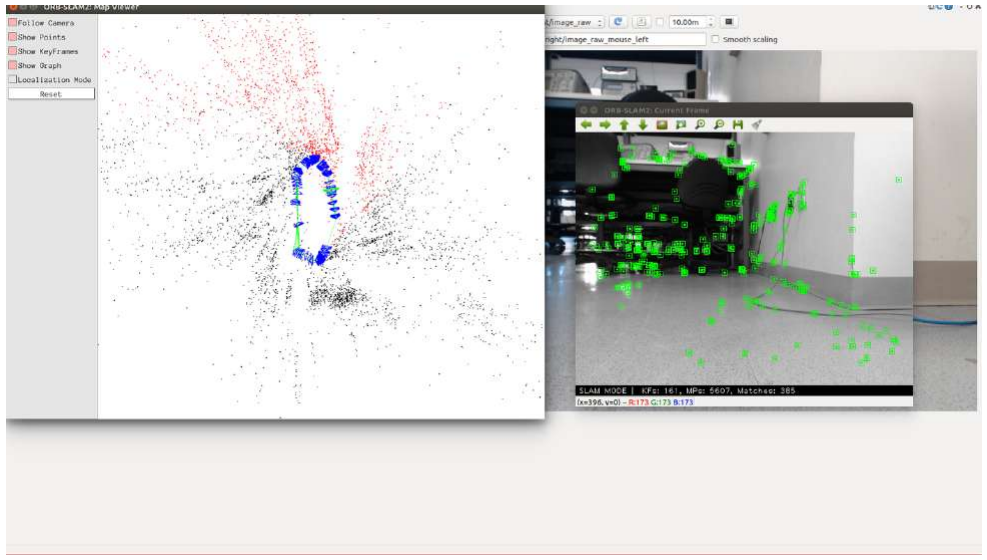
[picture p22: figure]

Figure 10: loop closure with ORBSLAM

### 5.6 RTAB Map Results

While ORBSLAM can provide good and robust Odometry in realtime, RTAB can create a good 3D point cloud of the environment and a occupancy grid. It does this by using rectified images from stereo image proc and odometry. It projects the point onto a plane to create a occupancy grid. The settings for the height of obstacle can be changed and only objects of certain height can be treated ass obstacles. The occupancy grid created can be used for navigation.

Figure 11: Point Cloud of RTAB shows a chair on the side and a poster beside it rendered in 3D.

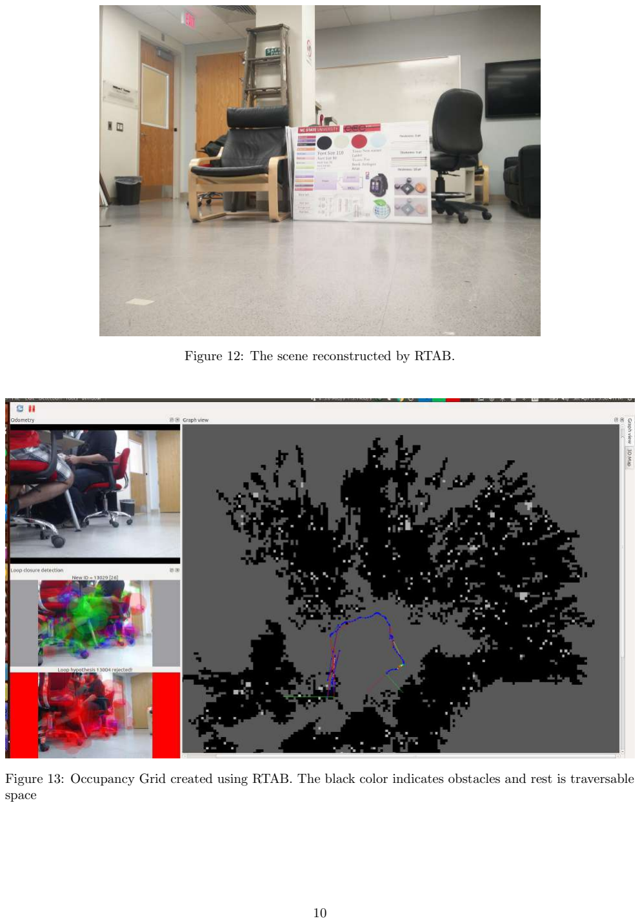
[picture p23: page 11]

Figure 12: The scene reconstructed by RTAB.

Figure 13: Occupancy Grid created using RTAB. The black color indicates obstacles and rest is traversable space

## 6 Conclusion

The problem statement was to implement a low cost Indoor SLAM for scanning an indoor area using a camera(s) and create a 3D reconstruction of its environment and also to create an occupancy grid or a traversable map. We were able to transform a two wheeled robot skeleton with motors and wheels into a robotic platform to stream stereo images to a remote computer and capable of controlling the motors on receiving commands form the remote computer. We were able to recreate the environment around the robot as a three dimensional point cloud. To achieve this level of performance, we had to create our own stereo camera rig using two monocular USB cameras. We implemented a python socket program to stream the video feed. We have implemented two SLAM techniques and compared their results for our robotic setup.

## 7 Appendices

### 7.1 GitHub repository

All source code and instructions to recreate the project can be accessed from the GitHub repository Indoor SLAM https://github.com/surajshanbhag/Indoor SLAM.git

### 7.2 Supplementary Images

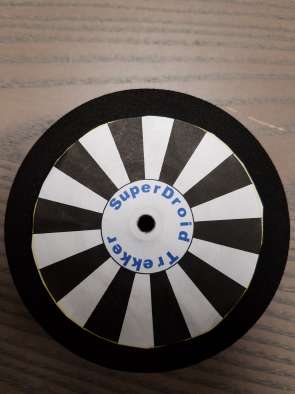
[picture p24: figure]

(a) Old encoder | (b) New encoder

Figure 14: Encoder stripes


Figure 15: URDF Model created for the project. Provides frame of references and transformation between wheels, cameras and the base of the robot.

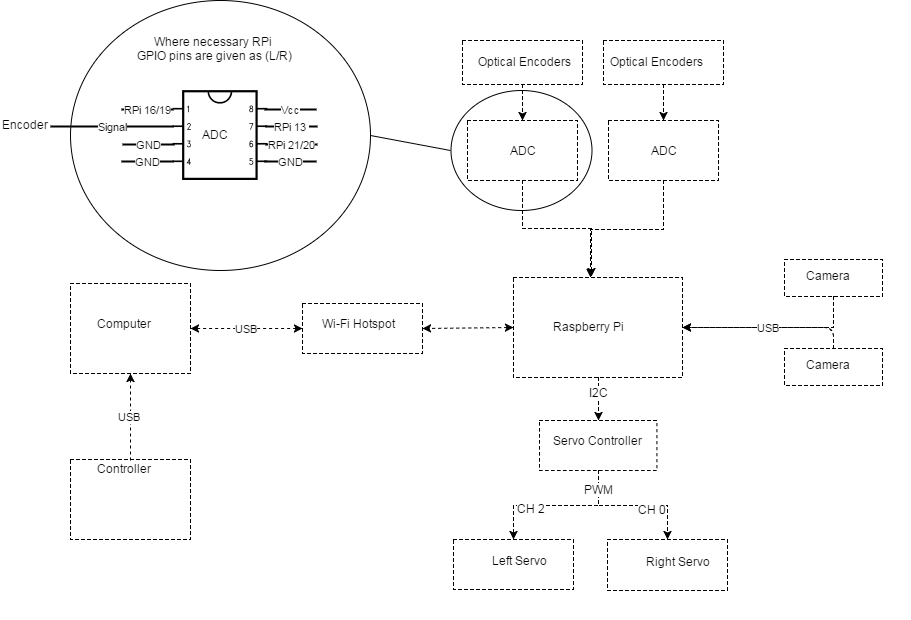
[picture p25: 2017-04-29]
doc/SLAM hardware.png

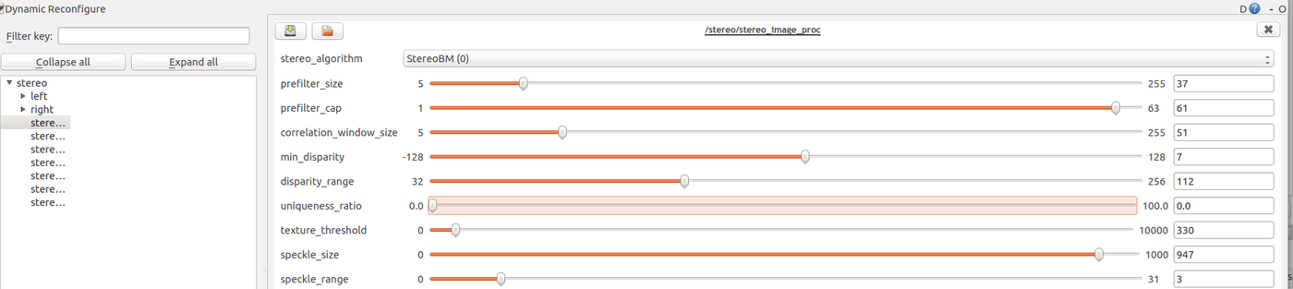
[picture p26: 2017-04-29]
doc/Images/PicFinalParameters.png

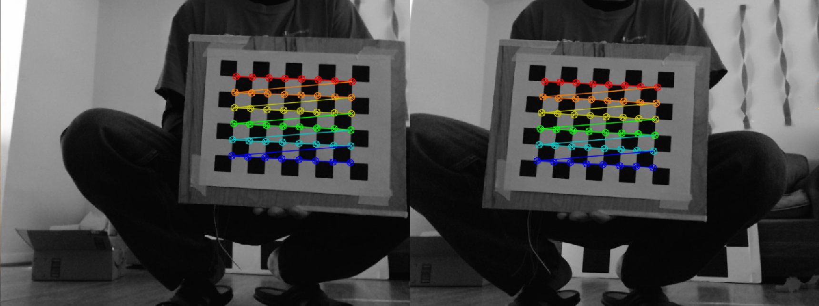
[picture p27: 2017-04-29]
doc/Images/stereo.png

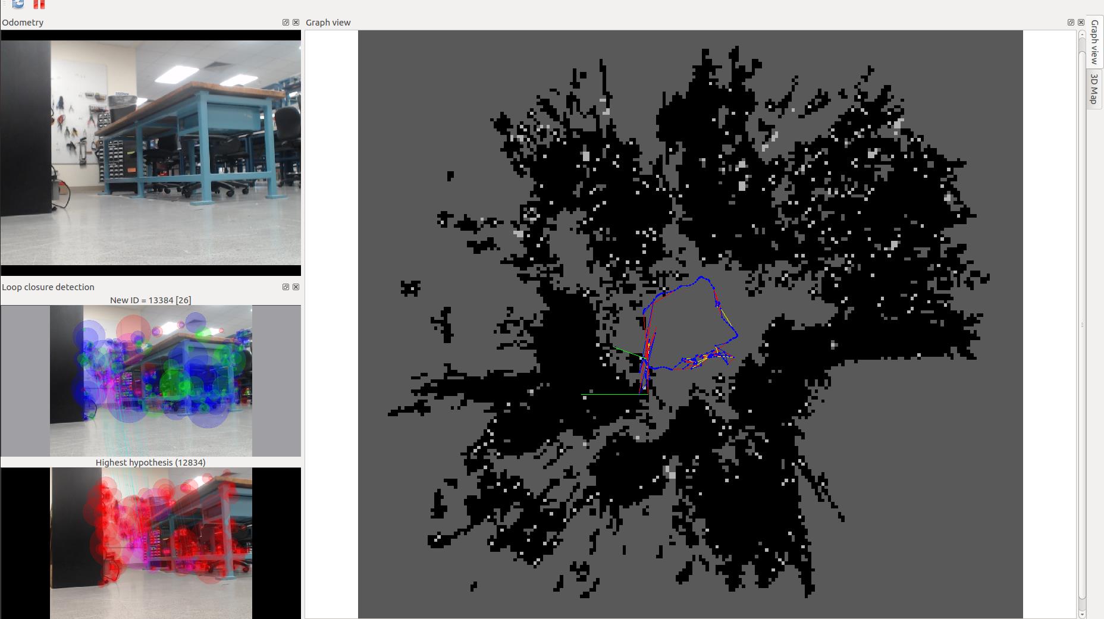
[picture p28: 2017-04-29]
doc/Images/2D with trajectory.jpg

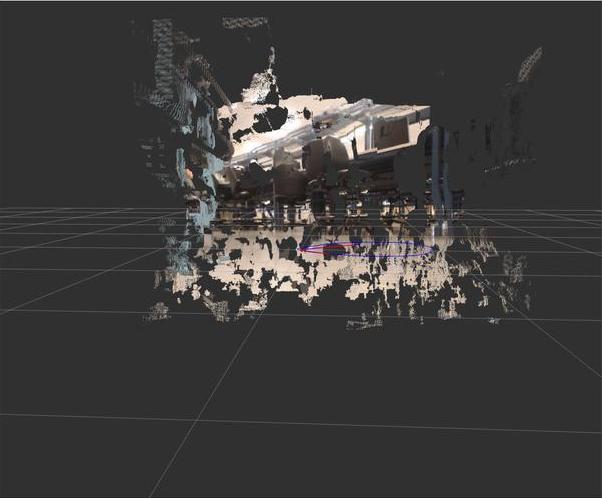
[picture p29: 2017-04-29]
doc/Images/3D-4.jpg

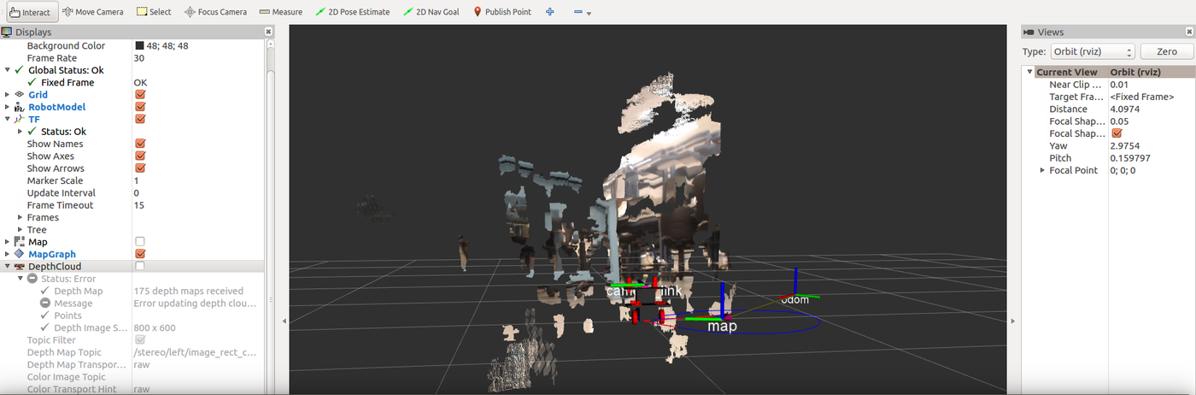
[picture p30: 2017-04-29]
doc/Images/PicFinal.png

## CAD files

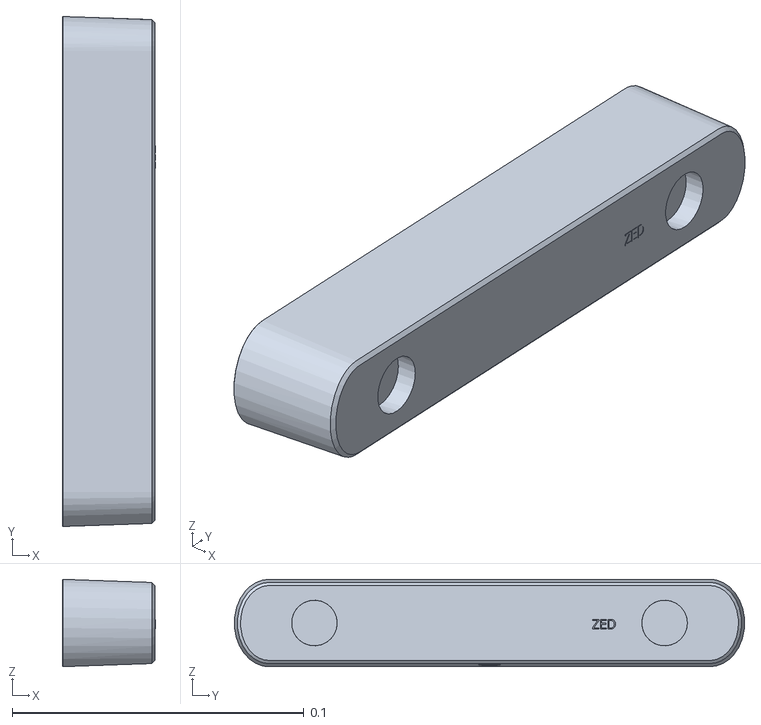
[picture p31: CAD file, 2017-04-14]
src/model/slam_model/meshes/ZED.stl
0.0318 x 0.175 x 0.0299

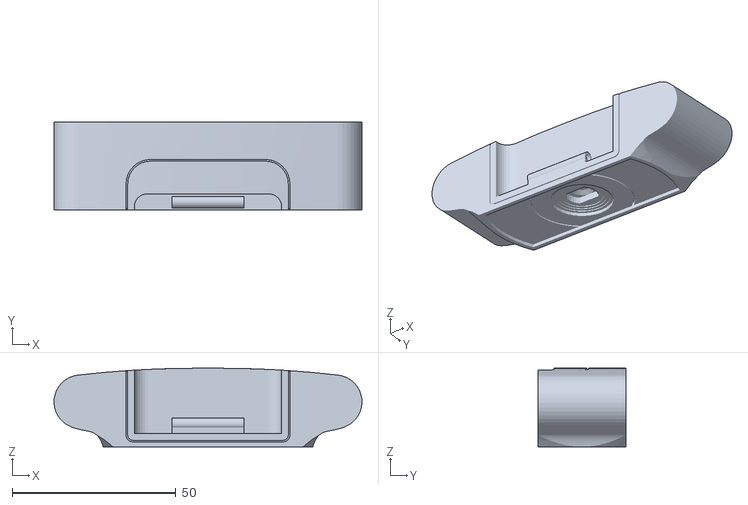
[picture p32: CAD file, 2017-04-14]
src/model/slam_model/meshes/Logitech_C920.stl
94.0 x 27.0 x 24.0

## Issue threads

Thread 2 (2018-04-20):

Error while executing streamer.py

r290085, 2018-04-20:
Hi
Thanks for publishing your work. I'm a ROS beginner from TAIWAN.
First of all, I ran "run_stereo_streamer.sh" and nothing happended, so I check every scripts.
I am getting "error" while running src/vision/stereoStreamer/streamer.py

The error is:
streamer(device=args['device'],"<broadcast>",client_port=int(args['port']),image_size=args['size'])
SyntaxError: non-keyword arg after keyword arg

I considered that in "streamer.py" line 102 ,"<broadcast>" missed someting.
Any suggestion to solve that problem?
Thanks.

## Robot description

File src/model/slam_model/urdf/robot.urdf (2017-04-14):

<?xml version="1.0"?>
<robot name="robot">
    <property name="M_PI" value="3.14159"/>

    <link name="chassis_footprint"/>
    <link name="chassis_base">
        <collision name='collision'>
            <geometry>
                <box size="2 0.5 1.5"/>
            </geometry>
        </collision>

        <visual name='visual'>
            <geometry>
                <box size="2 0.5 1.5"/>
            </geometry>
            <material name="white">
                <color rgba="1 1 1 0.8"/>
            </material>
        </visual>
    </link>
    <joint name="chassis_footprint_joint" type="fixed">
        <parent link="chassis_footprint"/>
        <child link="chassis_base"/>
        <origin xyz="0 0 0.95" rpy="0 0 0"/>
    </joint>
    <link name="chassis_extension_1">
        <collision name='collision'>
            <geometry>
                <box size="1 1 1.5"/>
            </geometry>
        </collision>

        <visual name='visual'>
            <geometry>
                <box size="1 1 1.5"/>
            </geometry>
            <material name="white">
                <color rgba="1 1 1 0.8"/>
            </material>
        </visual>
    </link>
    <joint name="chassis_extension_joint_1" type="fixed">
        <parent link="chassis_base"/>
        <child link="chassis_extension_1"/>
    </joint>
    <link name="chassis_extension_2">
        <collision name='collision'>
            <geometry>
                <box size="2 1 1"/>
            </geometry>
        </collision>

        <visual name='visual'>
            <geometry>
                <box size="2 1 1"/>
            </geometry>
            <material name="white">
                <color rgba="1 1 1 0.8"/>
            </material>
        </visual>
    </link>
    <joint name="chassis_extension_joint_2" type="fixed">
        <parent link="chassis_base"/>
        <child link="chassis_extension_2"/>
        <origin xyz="0 0 0.25" rpy="0 0 0"/>
    </joint>
    <link name="front_axel">
        <collision name='collision'>
            <geometry>
                <cylinder length="1" radius="0.05"/>
            </geometry>
        </collision>

        <visual name='visual'>
            <geometry>
                <cylinder length="1" radius="0.05"/>
            </geometry>
            <material name="grey">
                <color rgba="1 1 1 1"/>
            </material>
        </visual>
    </link>
    <link name="rear_axel">
        <collision name='collision'>
            <geometry>
                <cylinder length="1" radius="0.05"/>
            </geometry>
        </collision>

        <visual name='visual'>
            <geometry>
                <cylinder length="1" radius="0.05"/>
            </geometry>
            <material name="grey">
                <color rgba="1 1 1 1"/>
            </material>
        </visual>
    </link>
    <joint name="front_axel_joint" type="continuous">
        <parent link="chassis_base"/>
        <child link="front_axel"/>
        <origin xyz="0.8 0 -0.75" rpy="1.570 0 0"/>
        <axis xyz="0 0 1"/>
    </joint>
    <joint name="rear_axel_joint" type="continuous">
        <parent link="chassis_base"/>
        <child link="rear_axel"/>
        <origin xyz="-0.8 0 -0.75" rpy="1.570 0 0"/>
        <axis xyz="0 0 1"/>
    </joint>
    <link name="steered_wheel_left">
        <collision name='collision'>
            <geometry>
                <cylinder length="0.1" radius="0.2"/>
            </geometry>
        </collision>

        <visual name='visual'>
            <geometry>
                <cylinder length="0.1" radius="0.2"/>
            </geometry>
            <material name="black">
                <color rgba="0 0 0 1"/>
            </material>
        </visual>
    </link>
    <joint name="steered_wheel_left_joint" type="continuous">
        <parent link="front_axel"/>
        <child link="steered_wheel_left"/>
        <origin xyz="0 0 0.5" rpy="0 0 1.570"/>
        <axis xyz="0 1 1"/>
    </joint>
    <link name="steered_wheel_right">
        <collision name='collision'>
            <geometry>
                <cylinder length="0.1" radius="0.2"/>
            </geometry>
        </collision>

        <visual name='visual'>
            <geometry>
                <cylinder length="0.1" radius="0.2"/>
            </geometry>
            <material name="black">
                <color rgba="0 0 0 1"/>
            </material>
        </visual>
    </link>
    <joint name="steered_wheel_right_joint" type="continuous">
        <parent link="front_axel"/>
        <child link="steered_wheel_right"/>
        <origin xyz="0 0 -0.5" rpy="0 0 1.570"/>
        <axis xyz="0 1 1"/>
    </joint>
    <link name="power_wheel_left">
        <collision name='collision'>
            <geometry>
                <cylinder length="0.1" radius="0.2"/>
            </geometry>
        </collision>

        <visual name='visual'>
            <geometry>
                <cylinder length="0.1" radius="0.2"/>
            </geometry>
            <material name="black">
                <color rgba="0 0 0 1"/>
            </material>
        </visual>
    </link>
    <joint name="power_wheel_left_joint" type="continuous">
        <parent link="rear_axel"/>
        <child link="power_wheel_left"/>
        <origin xyz="0 0 0.5" rpy="0 0 1.570"/>
        <axis xyz="0 1 1"/>
    </joint>
    <link name="power_wheel_right">
        <collision name='collision'>
            <geometry>
                <cylinder length="0.1" radius="0.2"/>
            </geometry>
        </collision>

        <visual name='visual'>
            <geometry>
                <cylinder length="0.1" radius="0.2"/>
            </geometry>
            <material name="black">
                <color rgba="0 0 0 1"/>
            </material>
        </visual>
    </link>
    <joint name="power_wheel_right_joint" type="continuous">
        <parent link="rear_axel"/>
        <child link="power_wheel_right"/>
        <origin xyz="0 0 -0.5" rpy="0 0 1.570"/>
        <axis xyz="0 1 1"/>
    </joint>
    <link name="laser_scanner">
        <collision name='collision'>
            <geometry>
                <cylinder length="0.2" radius="0.08"/>
            </geometry>
        </collision>

        <visual name='visual'>
            <geometry>
                <cylinder length="0.2" radius="0.08"/>
            </geometry>
            <material name="red">
                <color rgba="1 0 0 1"/>
            </material>
        </visual>
    </link>
    <joint name="laser_scanner_joint" type="fixed">
        <parent link="chassis_base"/>
        <child link="laser_scanner"/>
        <origin xyz="1.08 0 0.3" rpy="0 0 0"/>
        <axis xyz="0 0 0 "/>
    </joint>
</robot>

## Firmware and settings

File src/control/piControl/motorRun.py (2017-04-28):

from __future__ import division
import motorDriver.pwm as pwm_mod
import time
import socket_class as socket
import sys
import numpy as np

speed=0.5
RMotorCh = None
LMotorCh = None

servo_min = None
servo_nut = None
servo_max = None



def pwm_setup():
    global RMotorCh,LMotorCh
    global servo_min,servo_nut,servo_max

    pwm = pwm_mod.PCA9685()
    #set frequency to 50 Hz
    pwm.set_pwm_freq(50)
    #p = 1/freq = 1/50 = 20ms
    #"tick" = 20ms / 4096 = 4.883us
    tick = 4.883

    #mim = 553us 553/4.886 = 113
    servo_min = 550/tick
    #max = 2520us 2520/4.886 = 516
    servo_max = 2550/tick
    #neuteral = 1536us 1536/4.886 = 314.47
    servo_nut = 1549/tick
    RMotorCh = 0
    LMotorCh = 2

    return pwm

def run_motors_call(pwm,R_vel, L_vel):
    """runs motors using Pi Servo hat
    receives input:
    PWM object - generated by motorDriver.py
    Right motor speed range (-1 to 1)
    left motor speed range (-1 to 1)
    """

    global RMotorCh,LMotorCh
    global servo_min,servo_nut,servo_max,speed
    
    #prevent motors from turning backwards to avoid confusing encoders 
    if R_vel < 0:
        R_vel = 0

    if L_vel < 0:
        L_vel = 0

    #ensure setup procedure was run
    if(RMotorCh is None or LMotorCh is  None):
        print("Motors not setup")
        return
    
    #calculate PWM from input
    R = int((((servo_max-servo_min)/2)*R_vel*speed+servo_nut))
    L = int((((servo_max-servo_min)/2)*-L_vel*speed+servo_nut))

    print(R,L)
    #send to hat
    pwm.set_pwm(RMotorCh,0,R)
    pwm.set_pwm(LMotorCh,0,L)


if __name__ == "__main__":
    """if this script is main it connects to a socket then passes motor values received to pi hat
       script defaults to looking for socket at 10.42.0.1 on port 50676, this can be overwritten by passing in 2 arguments
       first the IP of the server then the port to send information on"""
    #generate pwm object
    pwm = pwm_setup()
    print("Starting Test")
    
    #start socket
    s = socket.initSocket()
    
    while True:
        try:
            if len(sys.argv) == 3:
                socket.connect(s,sys.argv[1],int(sys.argv[2]))
            else:
                socket.connect(s,"10.42.0.1",50676)
            break
        except:
            pass
        
        
    while True:
        rec = s.recv(4096)
        if(rec == "stop"):
            break
        s.send("OK")
        R,L = rec.split(",")
        R = np.float32(R)
        L = np.float32(L)
        print(R,L)
        run_motors_call(pwm,R,L)
    print("Done")

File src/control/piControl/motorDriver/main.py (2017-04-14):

#! /usr/bin/env python

from __future__ import division
import time

# Import the PCA9685 module.
import pwm as pwm_mod


# Uncomment to enable debug output.
#import logging
#logging.basicConfig(level=logging.DEBUG)

# Initialise the PCA9685 using the default address (0x40).
pwm = pwm_mod.PCA9685()

# Alternatively specify a different address and/or bus:
#pwm = Adafruit_PCA9685.PCA9685(address=0x41, busnum=2)

# Configure min and max servo pulse lengths
servo_min = 150  # Min pulse length out of 4096
servo_max = 600  # Max pulse length out of 4096

# Helper function to make setting a servo pulse width simpler.
def set_servo_pulse(channel, pulse):
    pulse_length = 1000000    # 1,000,000 us per second
    pulse_length //= 60       # 60 Hz
    print('{0}us per period'.format(pulse_length))
    pulse_length //= 4096     # 12 bits of resolution
    print('{0}us per bit'.format(pulse_length))
    pulse *= 1000
    pulse //= pulse_length
    pwm.set_pwm(channel, 0, pulse)

def main():
    # Set frequency to 60hz, good for servos.
    pwm.set_pwm_freq(60)

    print('Moving servo on channel 0, press Ctrl-C to quit...')
    while True:
        # Move servo on channel O between extremes.
        pwm.set_pwm(0, 0, servo_min)
        time.sleep(1)
        pwm.set_pwm(0, 0, servo_max)
        time.sleep(1)

if(__mane__ == "__main__"):
    main()

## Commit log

2017-04-14 added robot model
    [LogitechC920Montaj.stl, Logitech_C920.SLDPRT, Logitech_C920.stl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]
2017-04-14 Added motor control and encoder files
2017-04-15 updaed motor pi
2017-04-15 odom published,
    [robot.urdf.xacro]
2017-04-17 re organized files
    [LogitechC920Montaj.stl, Logitech_C920.SLDPRT, Logitech_C920.stl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]
2017-04-17 fixed motor control scripts
2017-04-17 updated robot model
    [robot.urdf.xacro]
2017-04-18 updated motor for new ones
2017-04-21 updated encoder and motor scripts for new motor encoder pait
2017-04-22 updated for new motor, new encoder and script for motor only
2017-04-23 added calibration files, new motor/encoder udpates,
2017-04-28 calibrated motors and changed from broadcast to p2p
2017-04-28 removed unneccesssary stl files
    [LogitechC920Montaj.stl, Logitech_C920.SLDPRT]
